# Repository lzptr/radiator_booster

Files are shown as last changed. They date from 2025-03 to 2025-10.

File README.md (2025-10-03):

# Radiator Booster
ESP32C3 based fan control board for a modular  [3d printed radiator booster](https://www.printables.com/model/329566-heizkorperverstarker-mit-magnethalterung-radiator-?lang=de) based on this design.
The idea is to use ESPHome with Home Assistant to turn on up to 5 radiator booster fans, when my smart thermostats are turning on, and use a Home Assistant automation to keep them running for an hour and automatically shut them off after that.

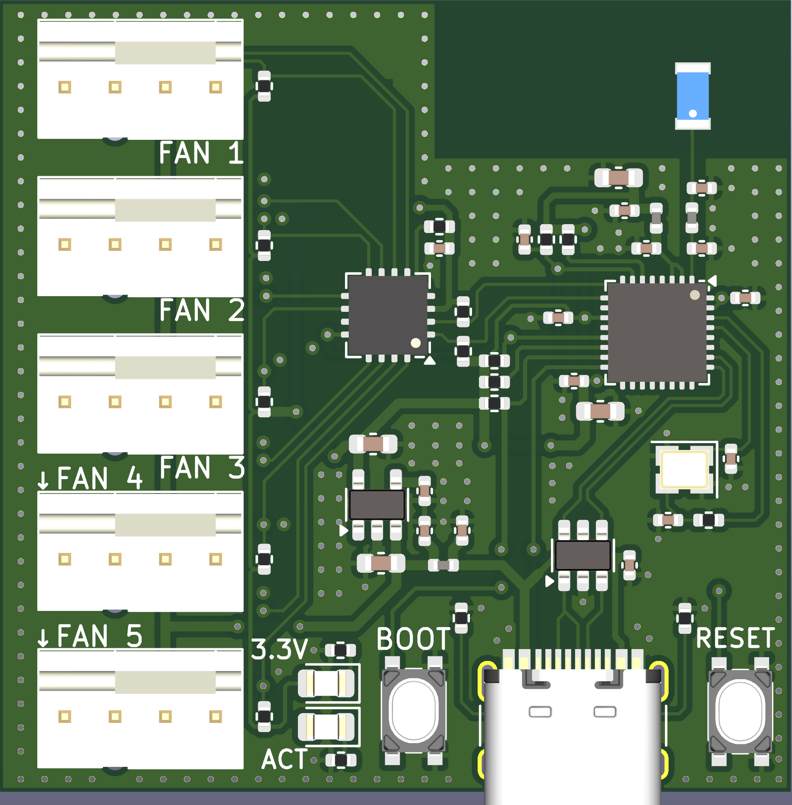
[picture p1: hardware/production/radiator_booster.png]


For an interactive KiCad experience see:
[Radiator Booster](https://kicanvas.org/?github=https://github.com/lzptr/radiator_booster/tree/main/hardware).



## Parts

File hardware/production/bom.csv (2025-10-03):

Designator | Footprint | Quantity | Value | LCSC Part #
AE301 | ANT3216LL00R2400A | 1 | ANT3216LL00R2400A | C293767
C201, C202, C204, C306, C307, C308, C309, C310, C311, C313, C401 | 0402 | 11 | 100n | C1525
C203, C205, C305, C312 | 0603 | 4 | 10u | C19702
C301, C303 | 0402 | 2 | 10pF | C32949
C302, C304 | 0402 | 2 | 3p | C1564
D201 | 0805 | 1 | 3.3V | C2297
D301 | 0805 | 1 | RUN | C2297
J301 | USB_C_Receptacle_HRO_TYPE-C-31-M-12 | 1 | USB_C_Receptacle_USB2.0 | C165948
J401 | FanPinHeader_1x04_P2.54mm_Vertical | 1 | Fan1 | C240840
J402 | FanPinHeader_1x04_P2.54mm_Vertical | 1 | Fan2 | C240840
J403 | FanPinHeader_1x04_P2.54mm_Vertical | 1 | Fan3 | C240840
J404 | FanPinHeader_1x04_P2.54mm_Vertical | 1 | Fan4 | C240840
J405 | FanPinHeader_1x04_P2.54mm_Vertical | 1 | Fan5 | C240840
L201, L301, L302 | 0402 | 3 | 2n2 | C412264
R201, R308 | 0402 | 2 | 1k | C11702
R301, R302, R304, R305, R306, R307 | 0402 | 6 | 5k1 | C25905
R303 | 0402 | 1 | 22R | C25092
R401, R402 | 0402 | 2 | 10k | C25744
R403, R404, R405, R406, R407, R408, R409 | 0402 | 7 | 2k2 | C25879
SW301 | SW_TL3365AF180QG | 1 | RESET | C2886926
SW302 | SW_TL3365AF180QG | 1 | BOOT | C2886926
U201 | SOT-23-5 | 1 | SPX3819M5-L-3-3 | C9055
U301 | SOT-23-6 | 1 | USBLC6-2SC6 | C5261088
U302 | QFN-32-1EP_5x5mm_P0.5mm_EP3.45x3.45mm | 1 | ESP32-C3FH4 | C2858491
U401 | QFN-16-1EP_4x4mm_P0.65mm_EP2.1x2.1mm | 1 | EMC2305-1-AP-TR
Y301 | Crystal_SMD_2520-4Pin_2.5x2.0mm | 1 | 40 MHz | C426970

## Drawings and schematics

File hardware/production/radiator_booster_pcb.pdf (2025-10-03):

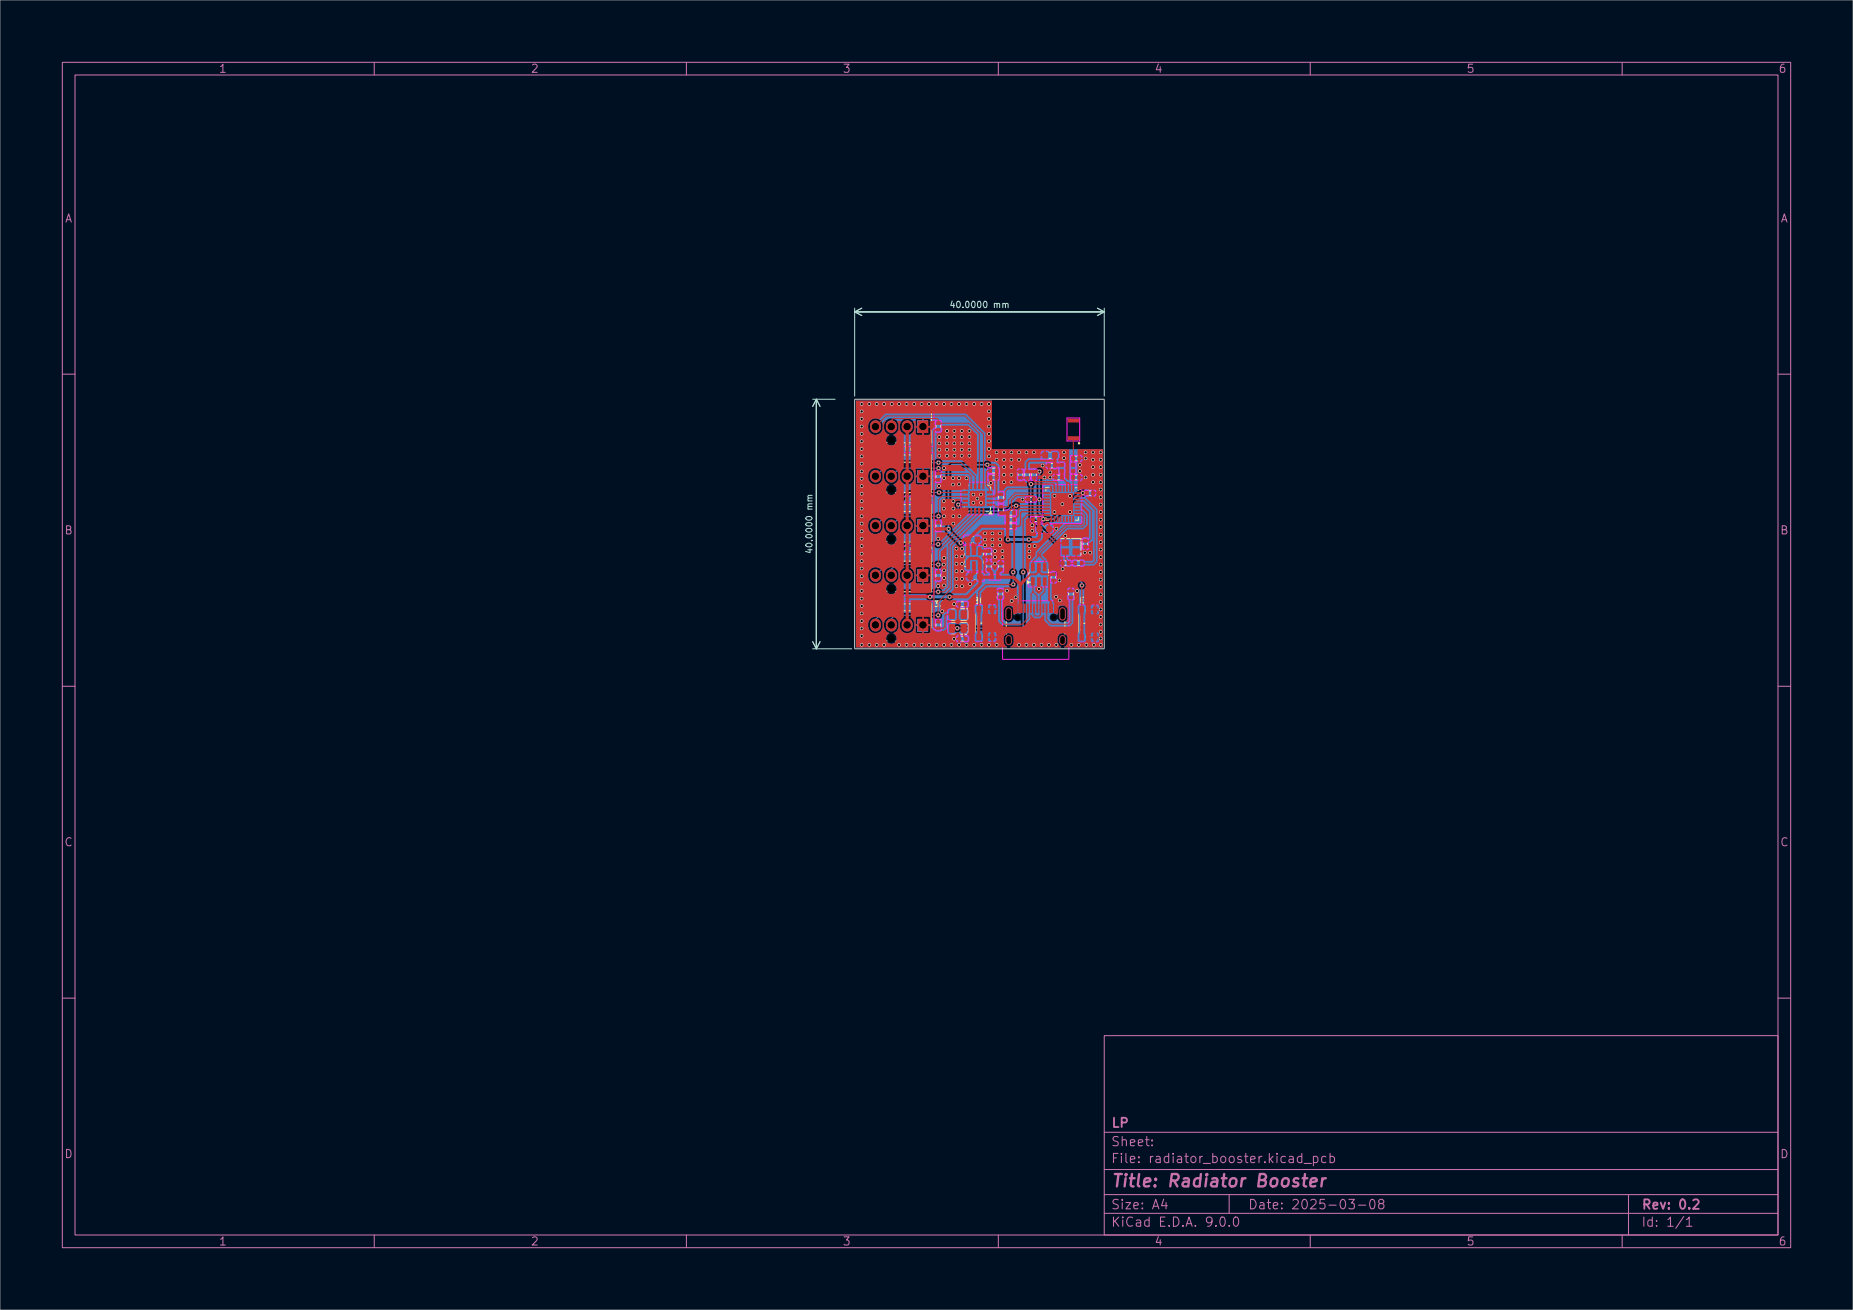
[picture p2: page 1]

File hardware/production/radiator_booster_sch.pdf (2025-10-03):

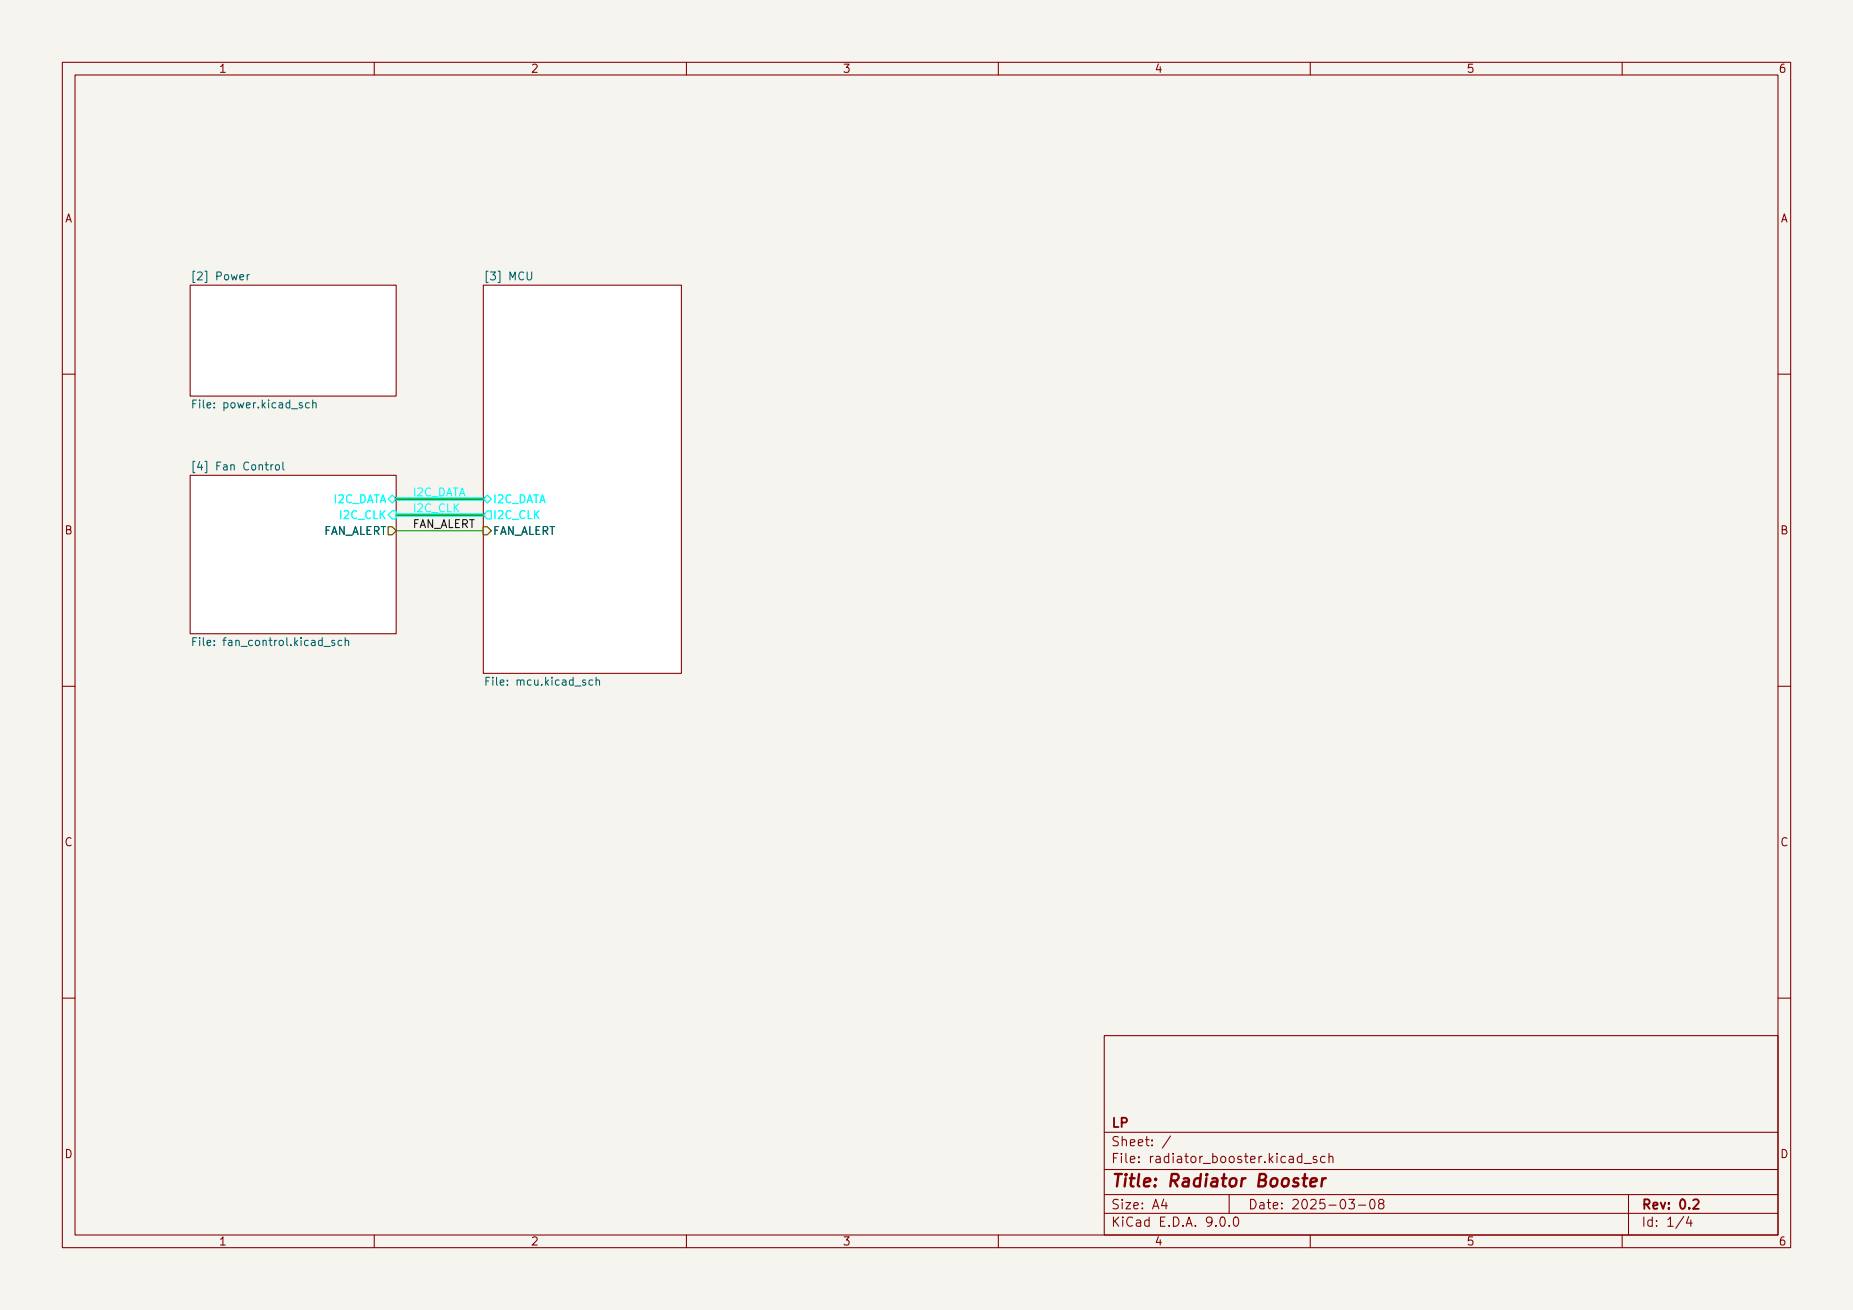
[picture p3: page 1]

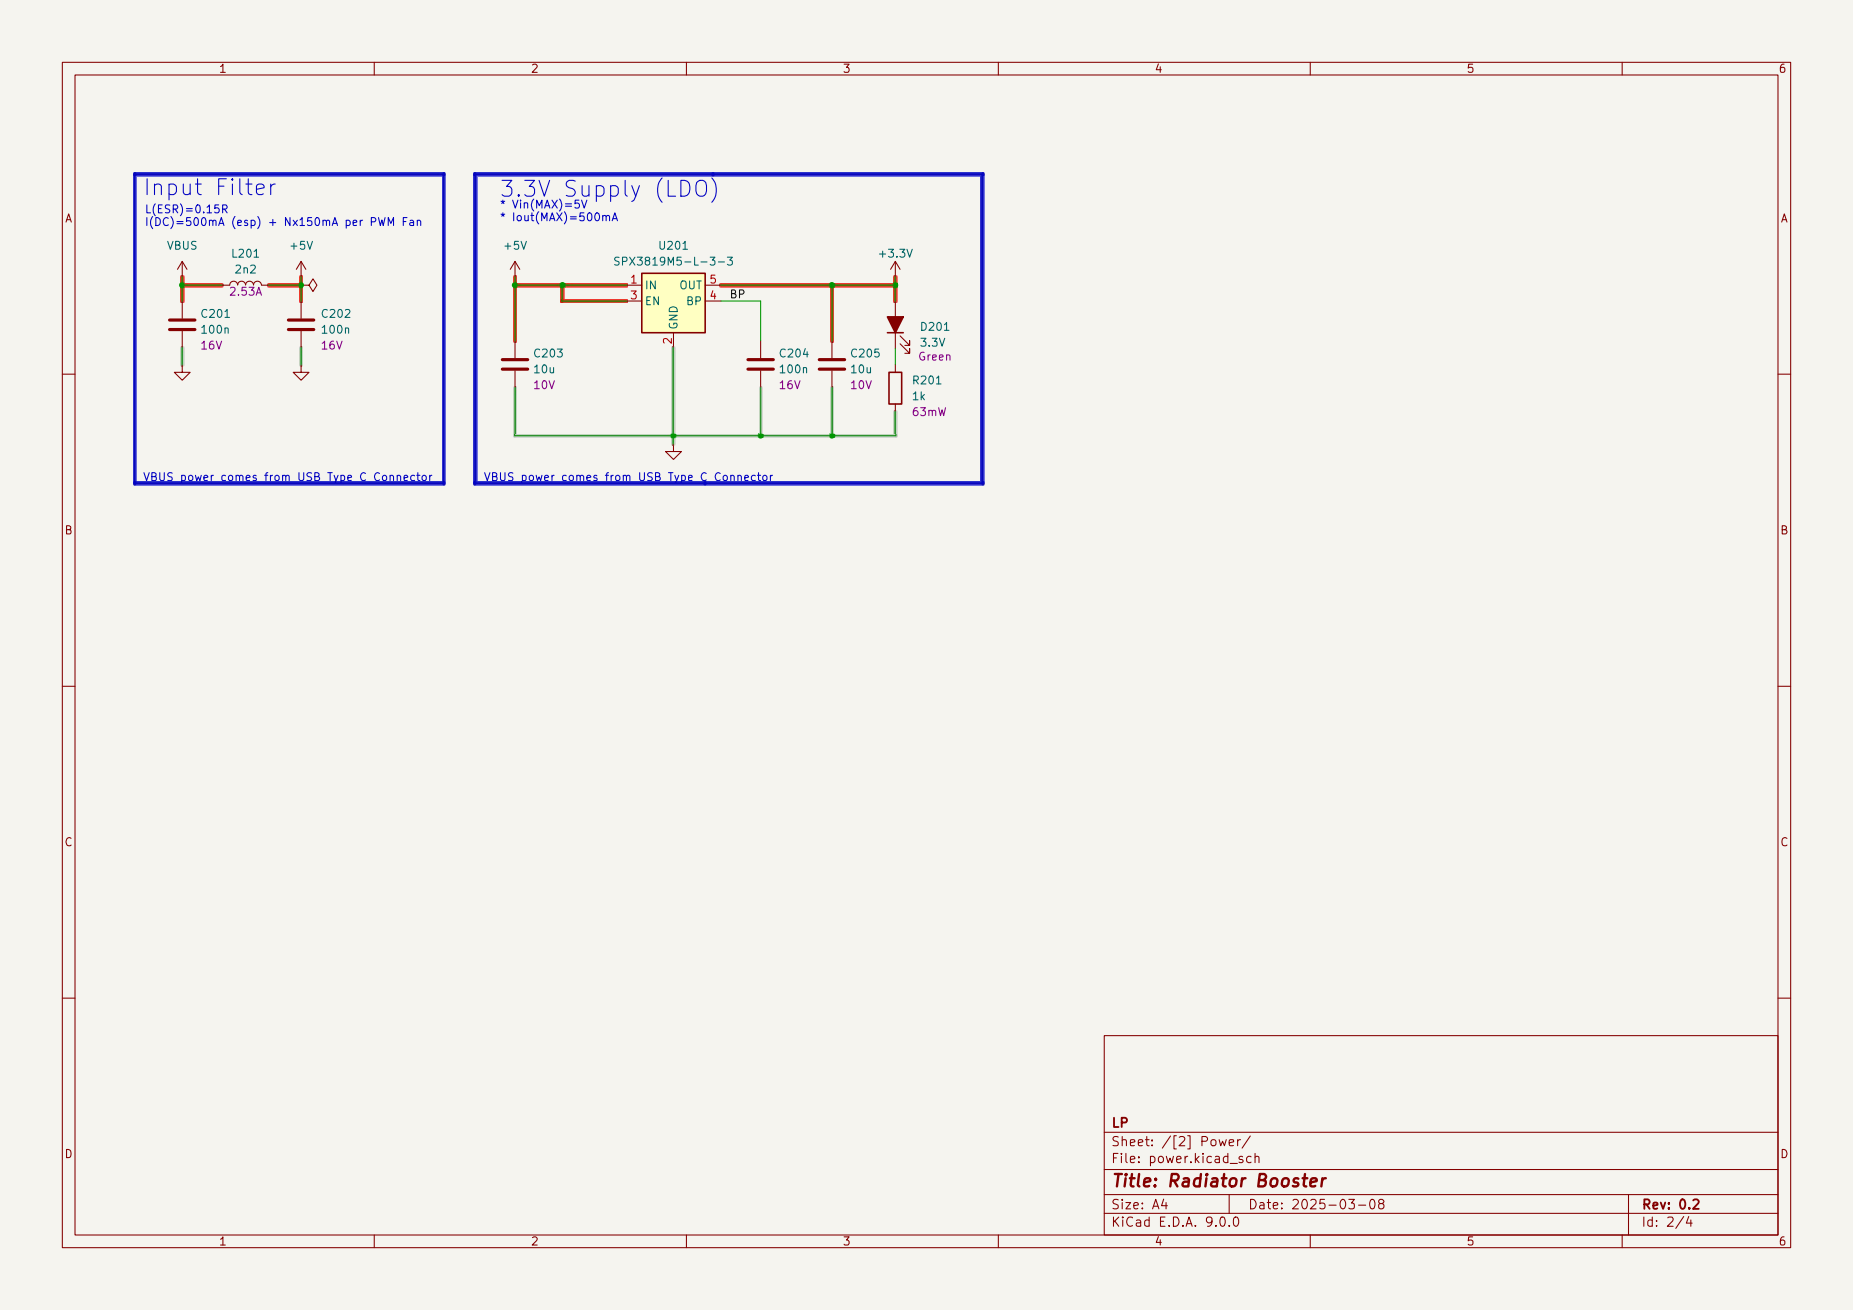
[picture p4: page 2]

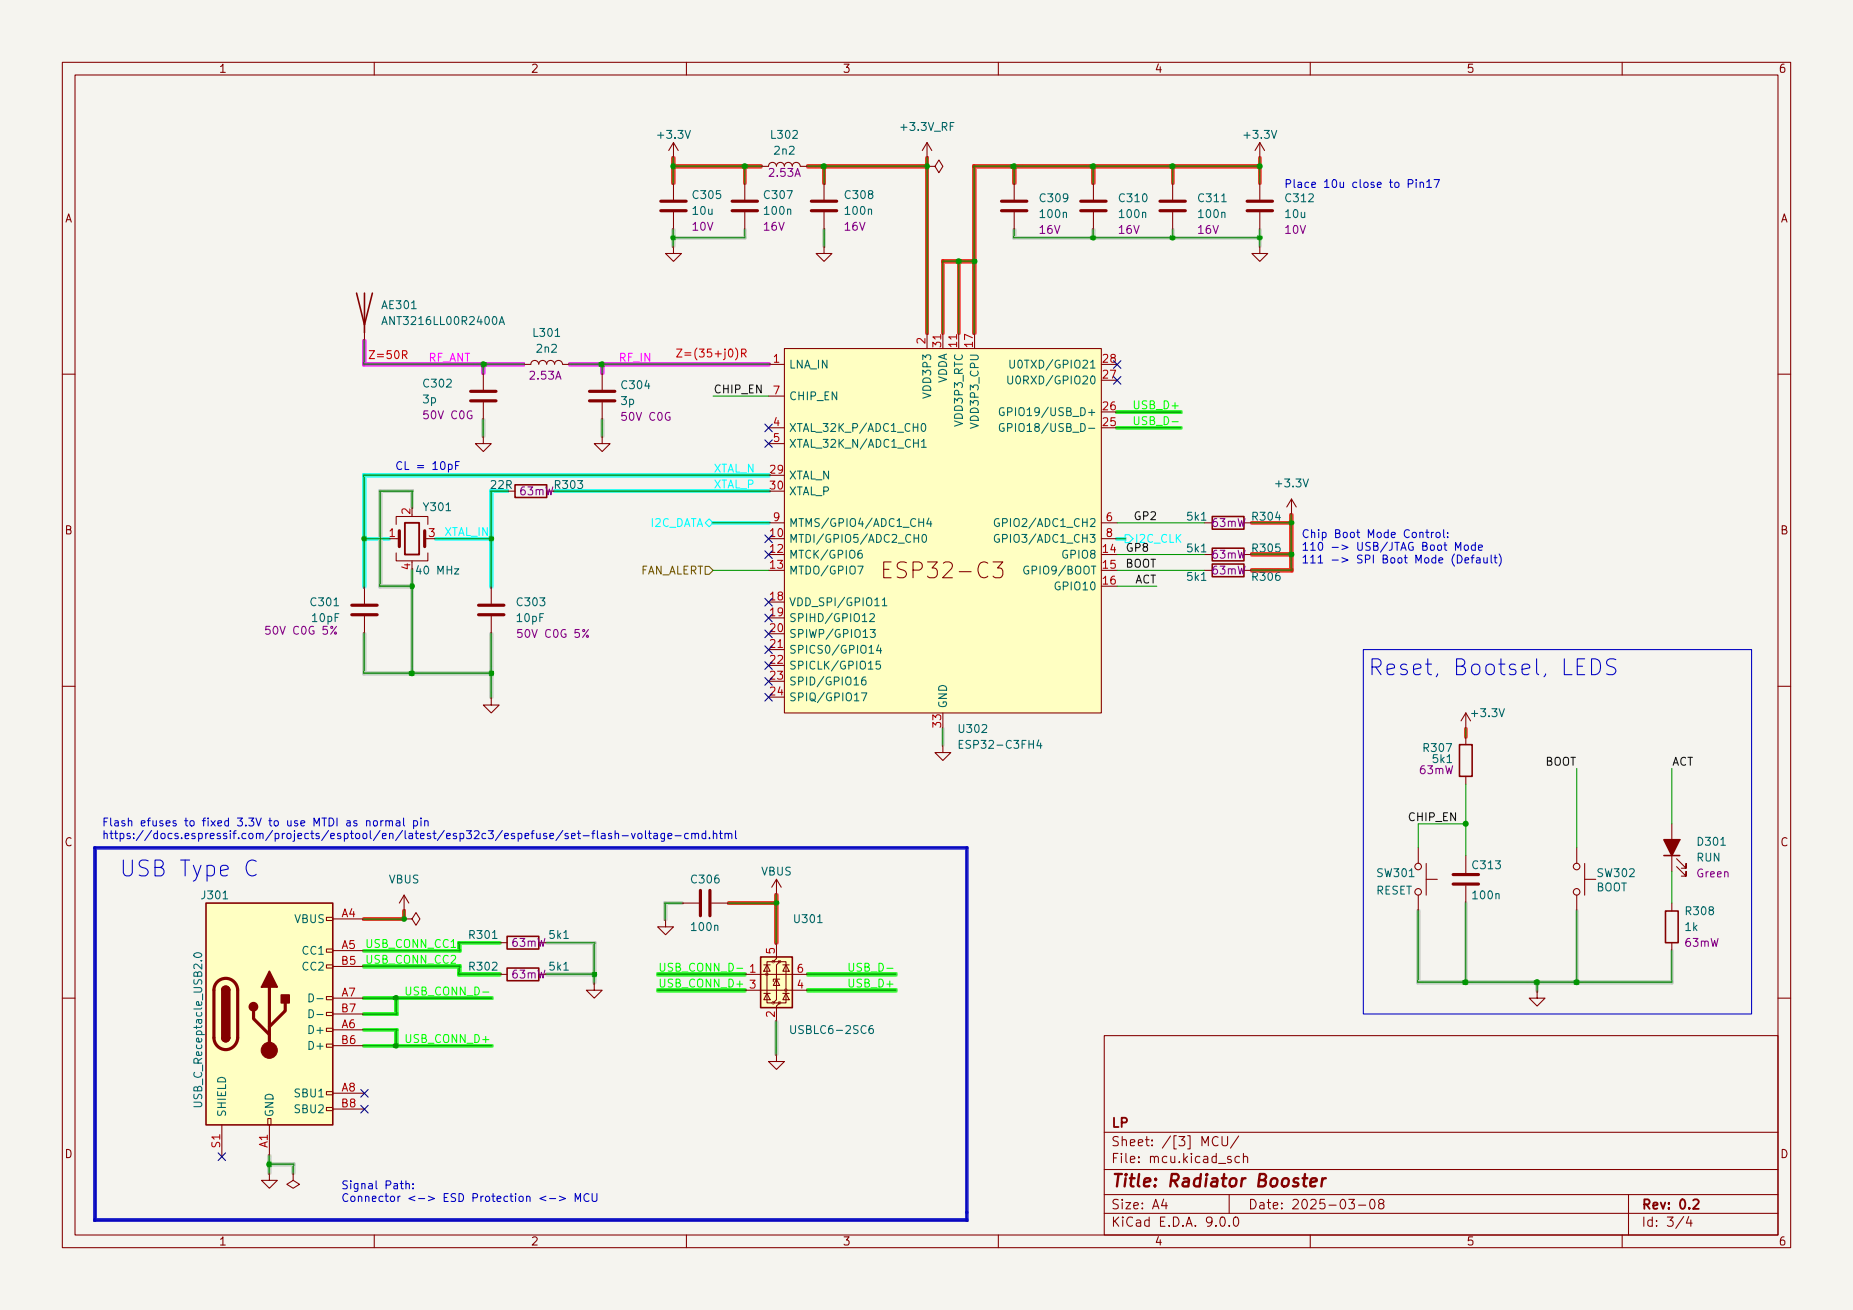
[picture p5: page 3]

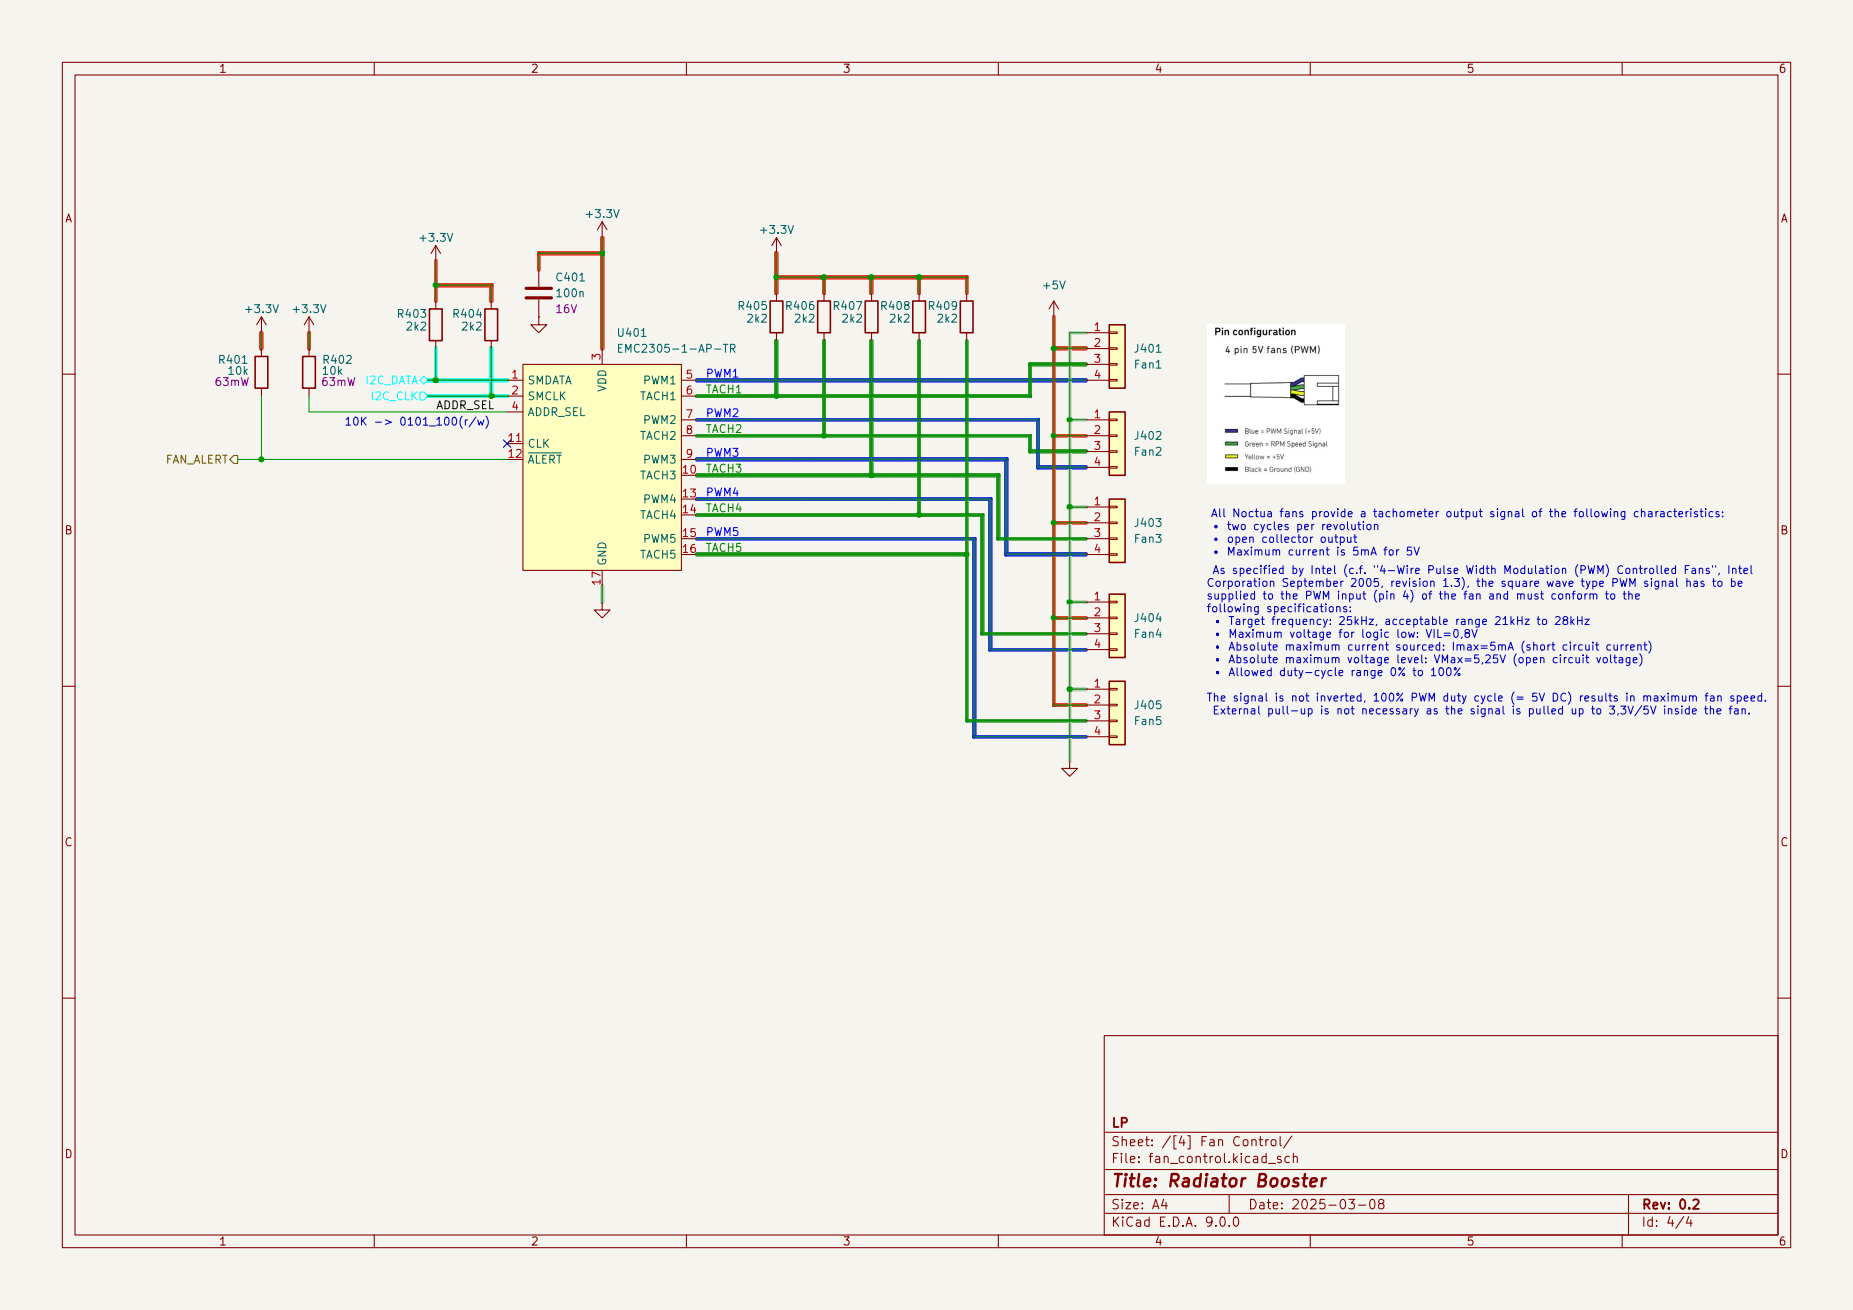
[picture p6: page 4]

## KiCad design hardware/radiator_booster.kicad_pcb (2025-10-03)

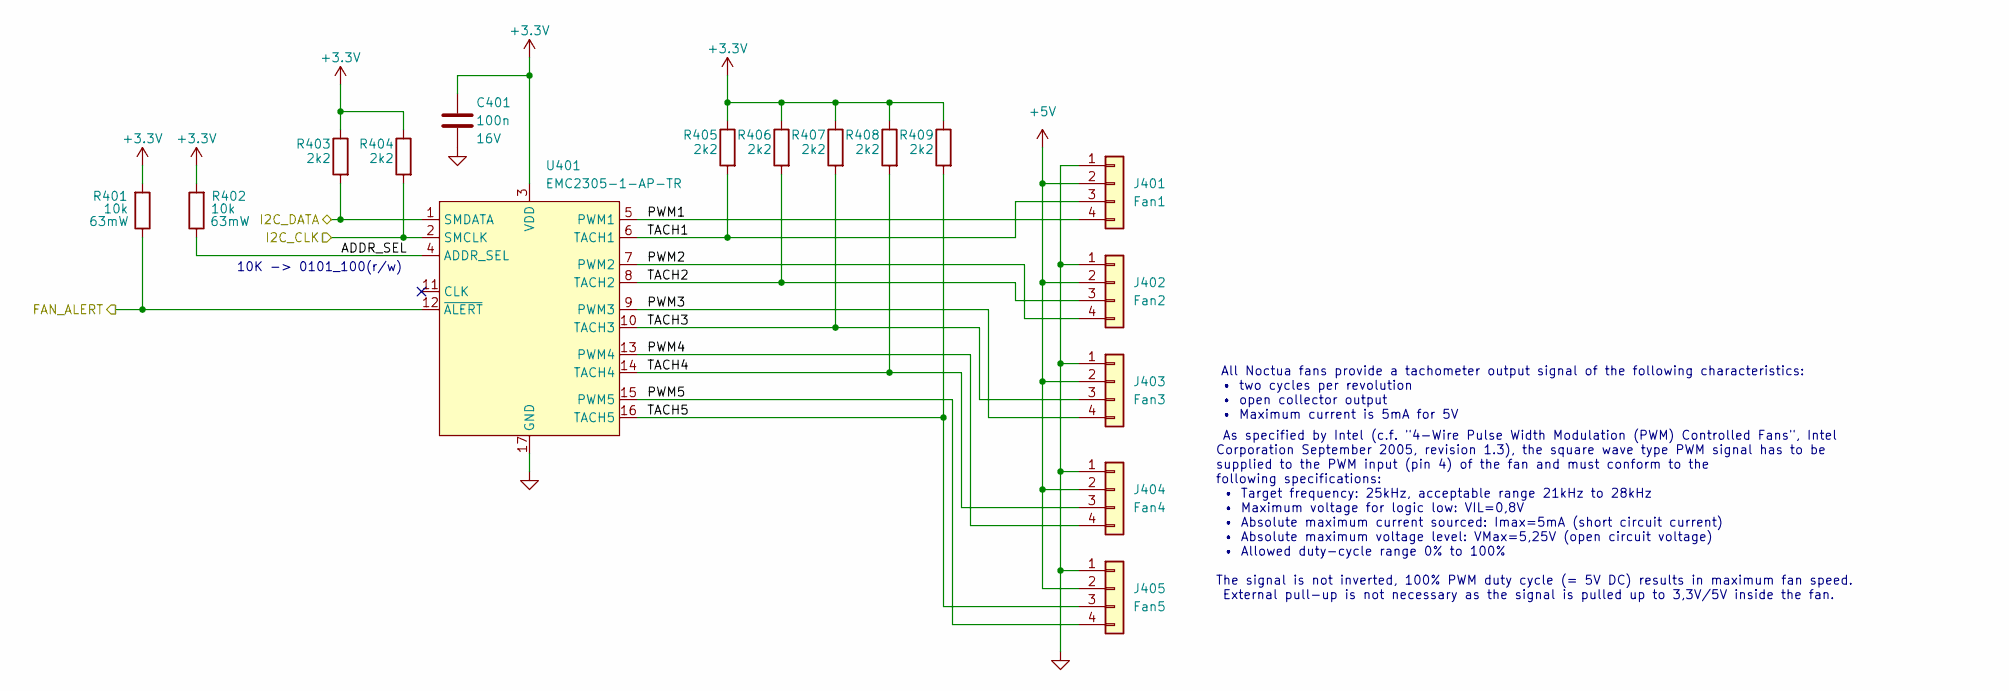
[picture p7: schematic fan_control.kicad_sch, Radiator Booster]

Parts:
C401: 100n; C_0402_1005Metric; Rating 16V; MPN C1525
J401: Fan1; FanPinHeader_1x04_P2.54mm_Vertical; MPN C240840
J402: Fan2; FanPinHeader_1x04_P2.54mm_Vertical; MPN C240840
J403: Fan3; FanPinHeader_1x04_P2.54mm_Vertical; MPN C240840
J404: Fan4; FanPinHeader_1x04_P2.54mm_Vertical; MPN C240840
J405: Fan5; FanPinHeader_1x04_P2.54mm_Vertical; MPN C240840
R401, R402: 10k; R_0402_1005Metric; Rating 63mW; MPN C25744
R403, R404, R405, R406, R407, R408, R409: 2k2; R_0402_1005Metric; Rating 63mW; MPN C25879
U401: EMC2305-1-AP-TR; QFN-16-1EP_4x4mm_P0.65mm_EP2.1x2.1mm

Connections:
+3.3V: C401.1, R401.2, R402.2, R403.1, R404.1, R405.1, R406.1, R407.1, R408.1, R409.1, U401.3 (VDD); also elsewhere on the board
+5V: J401.2, J402.2, J403.2, J404.2, J405.2; also elsewhere on the board
/FAN_ALERT: R401.1, U401.12 (~ALERT); also elsewhere on the board
/I2C_CLK: R404.2, U401.2 (SMCLK); also elsewhere on the board
/I2C_DATA: R403.2, U401.1 (SMDATA); also elsewhere on the board
/[4] Fan Control/ADDR_SEL: R402.1, U401.4 (ADDR_SEL)
/[4] Fan Control/PWM1: J401.4, U401.5 (PWM1)
/[4] Fan Control/PWM2: J402.4, U401.7 (PWM2)
/[4] Fan Control/PWM3: J403.4, U401.9 (PWM3)
/[4] Fan Control/PWM4: J404.4, U401.13 (PWM4)
/[4] Fan Control/PWM5: J405.4, U401.15 (PWM5)
/[4] Fan Control/TACH1: J401.3, R405.2, U401.6 (TACH1)
/[4] Fan Control/TACH2: J402.3, R406.2, U401.8 (TACH2)
/[4] Fan Control/TACH3: J403.3, R407.2, U401.10 (TACH3)
/[4] Fan Control/TACH4: J404.3, R408.2, U401.14 (TACH4)
/[4] Fan Control/TACH5: J405.3, R409.2, U401.16 (TACH5)
GND: C401.2, J401.1, J402.1, J403.1, J404.1, J405.1, U401.17 (GND); also elsewhere on the board

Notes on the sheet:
All Noctua fans provide a tachometer output signal of the following characteristics: • two cycles per revolution • open collector output • Maximum current is 5mA for 5V
10K -> 0101_100(r/w)
As specified by Intel (c.f. "4-Wire Pulse Width Modulation (PWM) Controlled Fans", Intel Corporation September 2005, revision 1.3), the square wave type PWM signal has to be supplied to the PWM input (pin 4) of the fan and must conform to the following specifications: • Target frequency: 25kHz, acc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

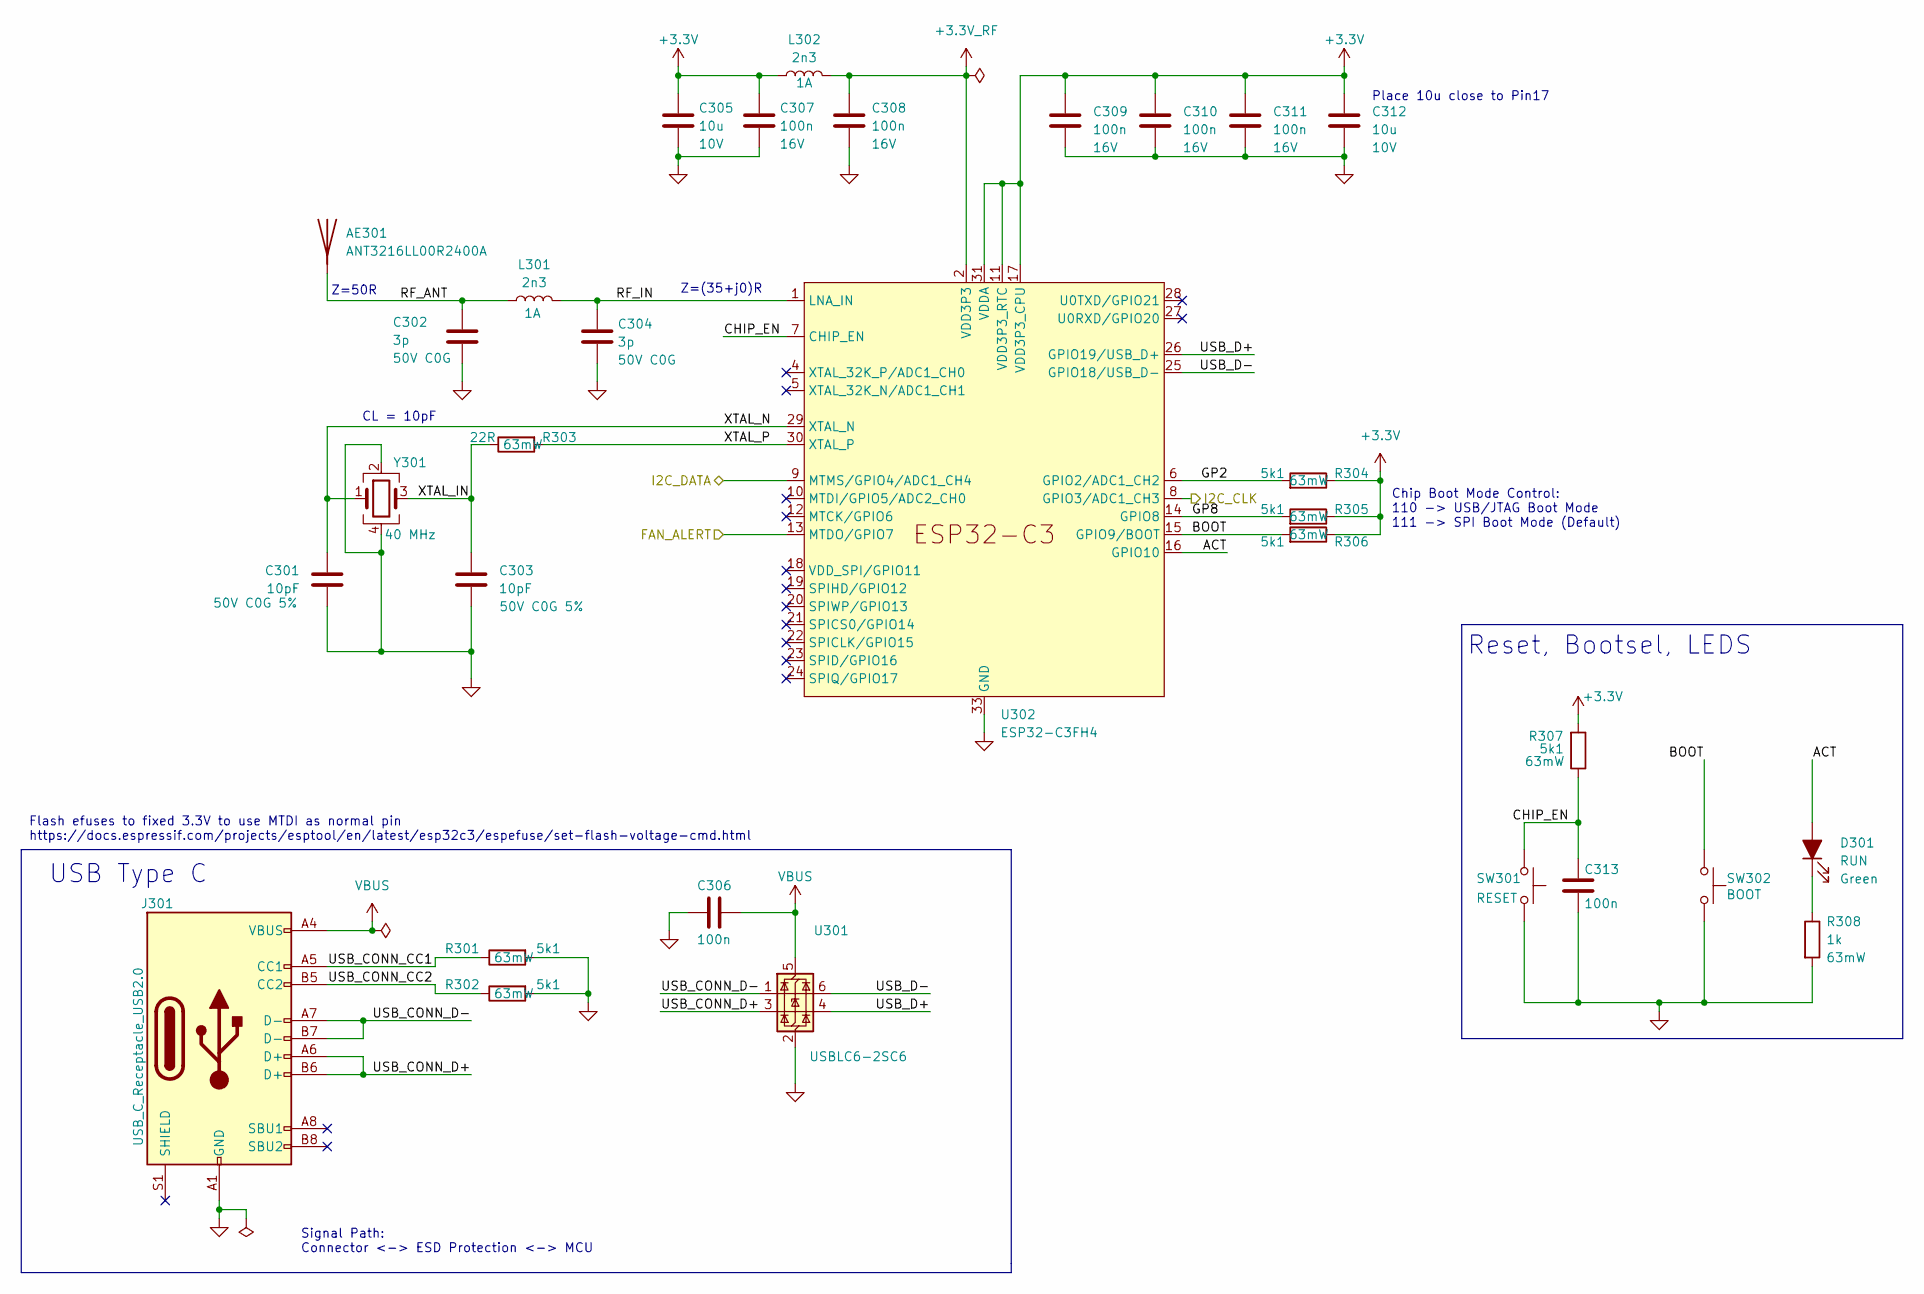
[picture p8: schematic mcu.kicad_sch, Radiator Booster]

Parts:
AE301: ANT3216LL00R2400A; MPN C293767
C301, C303: 10pF; C_0402_1005Metric; Rating 50V C0G 5%; MPN C32949
C302, C304: 3p; C_0402_1005Metric; Rating 50V C0G; MPN C88891
C305, C312: 10u; C_0603_1608Metric; Rating 10V; MPN C19702
C306, C307, C308, C309, C310, C311, C313: 100n; C_0402_1005Metric; Rating 16V; MPN C1525
D301: RUN; LED_0805_2012Metric; Rating Green; MPN C2297
J301: USB_C_Receptacle_USB2.0; USB_C_Receptacle_HRO_TYPE-C-31-M-12; MPN C165948
L301, L302: 2n3; L_0402_1005Metric; Rating 1A; MPN C412340
R301, R302, R304, R305, R306, R307: 5k1; R_0402_1005Metric; Rating 63mW; MPN C25905
R303: 22R; R_0402_1005Metric; Rating 63mW; MPN C25092
R308: 1k; R_0402_1005Metric; Rating 63mW; MPN C11702
SW301: RESET; SW_TL3365AF180QG; MPN C2886926
SW302: BOOT; SW_TL3365AF180QG; MPN C2886926
U301: USBLC6-2SC6; SOT-23-6; MPN C5261088
U302: ESP32-C3FH4; QFN-32-1EP_5x5mm_P0.5mm_EP3.45x3.45mm; MPN C2858491
Y301: 40 MHz; Crystal_SMD_2520-4Pin_2.5x2.0mm; MPN C426970

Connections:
+3.3V: C305.1, C307.1, C309.1, C310.1, C311.1, C312.1, L302.1, R304.1, R305.1, R306.1, R307.2, U302.11 (VDD3P3_RTC), U302.17 (VDD3P3_CPU), U302.31 (VDDA), U302.32 (VDDA); also elsewhere on the board
+3.3V_RF: C308.1, L302.2, U302.2 (VDD3P3), U302.3 (VDD3P3)
/FAN_ALERT: U302.13 (MTDO/GPIO7); also elsewhere on the board
/I2C_CLK: U302.8 (GPIO3/ADC1_CH3); also elsewhere on the board
/I2C_DATA: U302.9 (MTMS/GPIO4/ADC1_CH4); also elsewhere on the board
/[3] MCU/ACT: D301.2 (A), U302.16 (GPIO10)
/[3] MCU/BOOT: R306.2, SW302.1, U302.15 (GPIO9/BOOT)
/[3] MCU/CHIP_EN: C313.1, R307.1, SW301.1, U302.7 (CHIP_EN)
/[3] MCU/GP2: R304.2, U302.6 (GPIO2/ADC1_CH2)
/[3] MCU/GP8: R305.2, U302.14 (GPIO8)
/[3] MCU/RF_ANT: AE301.1 (A), C302.1, L301.1
/[3] MCU/RF_IN: C304.1, L301.2, U302.1 (LNA_IN)
/[3] MCU/USB_CONN_CC1: J301.A5 (CC1), R301.1
/[3] MCU/USB_CONN_CC2: J301.B5 (CC2), R302.1
/[3] MCU/USB_CONN_D+: J301.A6 (D+), J301.B6 (D+), U301.3 (I/O2)
/[3] MCU/USB_CONN_D-: J301.A7 (D-), J301.B7 (D-), U301.1 (I/O1)
/[3] MCU/USB_D+: U301.4 (I/O2), U302.26 (GPIO19/USB_D+)
/[3] MCU/USB_D-: U301.6 (I/O1), U302.25 (GPIO18/USB_D-)
/[3] MCU/XTAL_IN: C303.1, R303.1, Y301.3
/[3] MCU/XTAL_N: C301.1, U302.29 (XTAL_N), Y301.1
/[3] MCU/XTAL_P: R303.2, U302.30 (XTAL_P)
GND: C301.2, C302.2, C303.2, C304.2, C305.2, C306.2, C307.2, C308.2, C309.2, C310.2, C311.2, C312.2, C313.2, J301.A1 (GND), J301.A12 (GND), J301.B1 (GND), J301.B12 (GND), R301.2, R302.2, R308.2, SW301.2, SW302.2, U301.2 (GND), U302.33 (GND), Y301.2, Y301.4; also elsewhere on the board
unnamed: D301.1 (K), R308.1
VBUS: C306.1, J301.A4 (VBUS), J301.A9 (VBUS), J301.B4 (VBUS), J301.B9 (VBUS), U301.5 (VBUS); also elsewhere on the board

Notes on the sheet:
Z=50R
CL = 10pF
Chip Boot Mode Control: 110 -> USB/JTAG Boot Mode 111 -> SPI Boot Mode (Default)
Z=(35+j0)R
Reset, Bootsel, LEDS
Flash efuses to fixed 3.3V to use MTDI as normal pin https://docs.espressif.com/projects/esptool/en/latest/esp32c3/espefuse/set-flash-voltage-cmd.html
USB Type C
Signal Path: Connector <-> ESD Protection <-> MCU
Place 10u close to Pin17

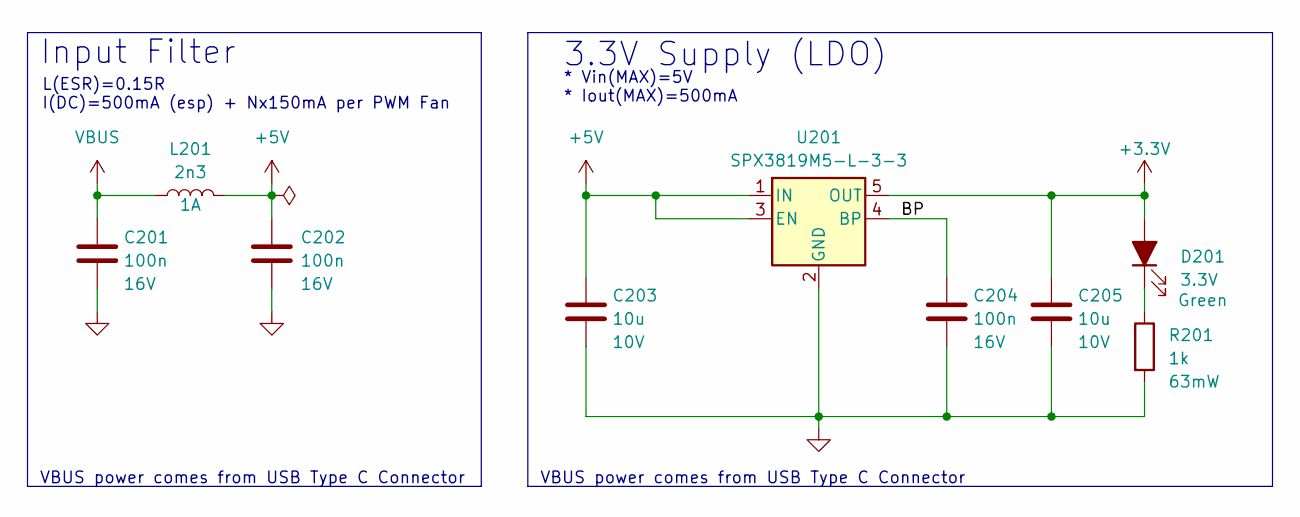
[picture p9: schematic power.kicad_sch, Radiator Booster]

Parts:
C201, C202, C204: 100n; C_0402_1005Metric; Rating 16V; MPN C1525
C203, C205: 10u; C_0603_1608Metric; Rating 10V; MPN C19702
D201: 3.3V; LED_0805_2012Metric; Rating Green; MPN C2297
L201: 2n3; L_0402_1005Metric; Rating 1A; MPN C412340
R201: 1k; R_0402_1005Metric; Rating 63mW; MPN C11702
U201: SPX3819M5-L-3-3; SOT-23-5; MPN C9055

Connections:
+3.3V: C205.1, D201.2 (A), U201.5 (OUT); also elsewhere on the board
+5V: C202.1, C203.1, L201.2, U201.1 (IN), U201.3 (EN); also elsewhere on the board
/[2] Power/BP: C204.1, U201.4 (BP)
GND: C201.2, C202.2, C203.2, C204.2, C205.2, R201.2, U201.2 (GND); also elsewhere on the board
unnamed: D201.1 (K), R201.1
VBUS: C201.1, L201.1; also elsewhere on the board

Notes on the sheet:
Input Filter
* Vin(MAX)=5V * Iout(MAX)=500mA
VBUS power comes from USB Type C Connector
L(ESR)=0.15R I(DC)=500mA (esp) + Nx150mA per PWM Fan
3.3V Supply (LDO)

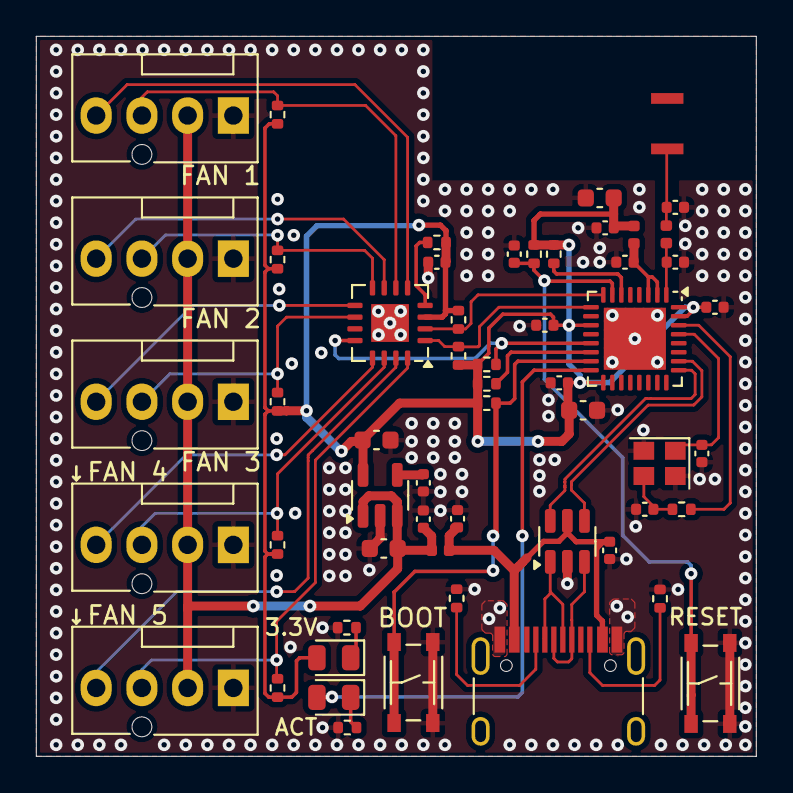
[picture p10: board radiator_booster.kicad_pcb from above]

Board: 4 copper layers, 40.0 x 40.0 mm, 56 parts (0 on the bottom side), 38 nets.

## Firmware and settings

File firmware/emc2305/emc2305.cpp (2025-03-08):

#include "emc2305.h"
#include "esphome/core/log.h"

namespace esphome {
namespace emc2305 {

static const char *const TAG = "emc2305";

void EMC2305Output::write_state(float state) {
  this->parent_->set_pwm_duty(this->fan_number_, state);
}

void EMC2305Component::setup() {
  ESP_LOGCONFIG(TAG, "Setting up EMC2305...");
  
  // Verify chip ID
  uint8_t chip_id;
  if (!this->read_byte(REG_PRODUCT_ID, &chip_id)) {
    ESP_LOGE(TAG, "Failed to read chip ID!");
    this->mark_failed();
    return;
  }
  
  if (chip_id != EMC2305_CHIP_ID) {
    ESP_LOGE(TAG, "Wrong chip ID! Expected: 0x%02X, got: 0x%02X", EMC2305_CHIP_ID, chip_id);
    this->mark_failed();
    return;
  }

  // Configure device
  uint8_t config = CONFIG_DIS_TO;  // Disable timeout for I2C compatibility
  if (!this->write_byte(REG_CONFIG, config)) {
    this->mark_failed();
    return;
  }
  
  // Set all PWM outputs to push-pull mode
  if (!this->write_byte(REG_PWM_OUTPUT, 0x1F)) {  // All 5 bits set
    this->mark_failed();
    return;
  }

  // Set 25kHz PWM frequency base for all fans
  if (!this->write_byte(REG_PWM_BASE, PWM_FREQ_25KHZ)) {
    this->mark_failed();
    return;
  }

  // Initialize all fans to 0%
  for (uint8_t i = 1; i <= 5; i++) {
    if (this->outputs_[i-1] != nullptr) {
      if (!this->write_byte(get_fan_reg_(i), 0)) {
        this->mark_failed();
        return;
      }
    }
  }
}

void EMC2305Component::dump_config() {
  ESP_LOGCONFIG(TAG, "EMC2305:");
  LOG_I2C_DEVICE(this);
  if (this->is_failed()) {
    ESP_LOGE(TAG, "Communication failed!");
    return;
  }
  
  for (uint8_t i = 0; i < 5; i++) {
    if (this->outputs_[i] != nullptr) {
      ESP_LOGCONFIG(TAG, "  Fan %d configured", i + 1);
    }
  }
}

EMC2305Output *EMC2305Component::create_fan_output(uint8_t fan_number) {
  if (fan_number < 1 || fan_number > 5) {
    ESP_LOGE(TAG, "Invalid fan number: %d", fan_number);
    return nullptr;
  }
  
  if (this->outputs_[fan_number - 1] != nullptr) {
    return this->outputs_[fan_number - 1];
  }
  
  auto *output = new EMC2305Output(this, fan_number);
  this->outputs_[fan_number - 1] = output;
  return output;
}

void EMC2305Component::set_pwm_duty(uint8_t fan_number, float duty) {
  if (fan_number < 1 || fan_number > 5) {
    ESP_LOGE(TAG, "Invalid fan number: %d", fan_number);
    return;
  }

  uint8_t pwm = duty * 255;
  if (!this->write_byte(get_fan_reg_(fan_number), pwm)) {
    ESP_LOGE(TAG, "Failed to set fan %d PWM duty cycle", fan_number);
    this->status_set_warning();
  }
}

}  // namespace emc2305
}  // namespace esphome

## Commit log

2024-12-20 Finished the schematic
    [fan_control.kicad_sch, mcu.kicad_sch, power.kicad_sch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]
2024-12-29 WIP pcb layout
    [fan_control.kicad_sch, mcu.kicad_sch, power.kicad_sch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]
2025-01-11 Finished the pcb layout
    [fan_control.kicad_sch, mcu.kicad_sch, power.kicad_sch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]
2025-01-19 release: v0.1
    [bom.csv, designators.csv, fan_control.kicad_sch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]
2025-03-08 Started work on rev 0.2
    [fan_control.kicad_sch, mcu.kicad_sch, power.kicad_sch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]
2025-03-09 Fixed routing at intel pwm fan connectors
    [fan_control.kicad_sch, mcu.kicad_sch, radiator_booster.kicad_pcb]
2025-03-17 Finished layout for rev 0.2
    [fan_control.kicad_sch, mcu.kicad_sch, power.kicad_sch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]
2025-03-18 Final touches
    [radiator_booster.kicad_pcb]
2025-03-18 Added production files
    [bom.csv, designators.csv, positions.csv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]
2025-03-22 Updated matching network. Changed inductor for all filter for bom sonsolidation after matching network changes
    [fan_control.kicad_sch, mcu.kicad_sch, power.kicad_sch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]
